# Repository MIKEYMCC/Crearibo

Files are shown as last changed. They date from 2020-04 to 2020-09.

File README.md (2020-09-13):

# Crearibo

CR-10 3D Printer Modification

This is a modification of the CR-10 S4 3D printer. It is a complete change to the Y X and Z axis to imitate the Prusa style printer specifically the Prusa MK2 and MK3 range. The main things provided by this modification are the parts for the Y and Z axis. THe X axis can be parts from the Prusa, Caribou and Bear range of pruse printers and modifications. There are 8mm and 10mm veriants of the Z axis. To be able to use the 10mm Z and or X axis currently you would need to use the Z and or X axis of the Caribou printer. I have included X motor and X idlers that have been modified to use the creality switches, these are for 8mm only, these were originally designed by Vekoj. 

The 10mm version does have a slightly smaller X axis at 295mm instead 300mm due to the way the X axis parts are designed.

To help with aligning the Y rods the holders edge should be 101mm from the edge of the extrusion with the endcap removed.

There is a template that can be printed to help drill holes in the CR-10 Y carriage so that the bearings can be attached.

Bill of Materials for 8mm

Z Axis:

6 x M4 10mm Cap Head Bolt FOR Z MOTOR MOUNTS

6 x M4 10mm Cap Head Bolt FOR Z TOP MOUNTS

16 x M4 Slot in T nuts

8 x M3 8mm Cap Head Bolt FOR MOTORS

2 x 535mmx8mm Linear Smooth Rods

4 x LM8UU Leanir Bearing

Y Axis:

2 x 12mmx500mm Linear Smooth Rods

3 x SCS12UU

12 x M5 10mm Cap Head Bolts FOR BEARING MOUNTING

5 x M3 10mm Cap Head Bolts

4 x M3 Locknuts FOR Y IDLER AND Y BELT HOLDER

4 x M4 10mm Cap Head Bolts FOR Y ROD HOLDERS

8 x M4 16mm Cap Head Bolts FOR Y ROD HOLDERS

16 x M4 Slot in T nuts

2 x M4 12mm Cap Head Bolts FOR Y IDLER

2 x M4 10mm Cap Head Bolts FOR Y MOTOR MOUNT

2 x M3 20mm Cap Head Bolts FOR Y IDLER ADJUSTER

1 x Microswitch for endstop

GT2 6mm Timing Belt

1 x 2GT 6mm Belt Timing Pulley 16T Toothless

1 x 2GT 6mm Belt Timing Pulley 16T Toothed to attach to motor

4 x Spacers for the bed to sit on.

4 x M3 12mm Cap Head Bolts for Y Carriage Belt Holder

4 x M3 Nut Square Y Carriage Belt Holder

X Axis:

2 x 415mmx8mm Linear Smooth Rods

3 x LM8UU Linear Bearinh

For the 10mm rod version you need 420mm long rods and bearings as specified by Caribou.

LCD Mounts:

2 x M4 10mm Cap Head Bolts

2 x M4 Slot in T nuts

Mosfet Case:

4 x M3 10mm Cap Head Bolts

4 x M3 8mm Cap Head Bolts

4 x M3 Square Nuts

4 x M3 Nut

1 x M4 10mm Cap Head Bolt

1 x M4 Slot in T nut

PSU case:

5 x M4 10mm Cap Head Bolts

5 x M4 Slot in T nut

4 x M4 8mm Counter Sunk Bolts

Bill of Materials for 10mm

Z Axis:

6 x M4 10mm Cap Head Bolt FOR Z MOTOR MOUNTS

8 x M4 10mm Cap Head Bolt FOR Z TOP MOUNTS

16 x M4 Slot in T nuts

8 x M3 8mm Cap Head Bolt FOR MOTORS

2 x 535mmx10mm Linear Smooth Rods

2 x LM10LUU Linear Bearing

Firmware

Is not currently provided as there can be differences in the mainboards used. I am personally using an SKR 1.4 Turbo and the firmware created by Chris Warkocki for the Bear can be used with changes to the axis lengths.

A lot of this mod has been made possible by the work of other groups and people namely Prusa, Caribou, Vekoj (thingiverse name) and Bear.

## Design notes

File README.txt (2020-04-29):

Crearibo Creality CR-10 Conversion to Linear Rods + 10mm Z/X version by MIKEYMCC on Thingiverse: https://www.thingiverse.com/thing:3143998

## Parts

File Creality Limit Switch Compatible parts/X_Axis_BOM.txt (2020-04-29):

X Axis:
2 x 415mmx8mm Linear Smooth Rods
3 x LM8UU Linear Bearing

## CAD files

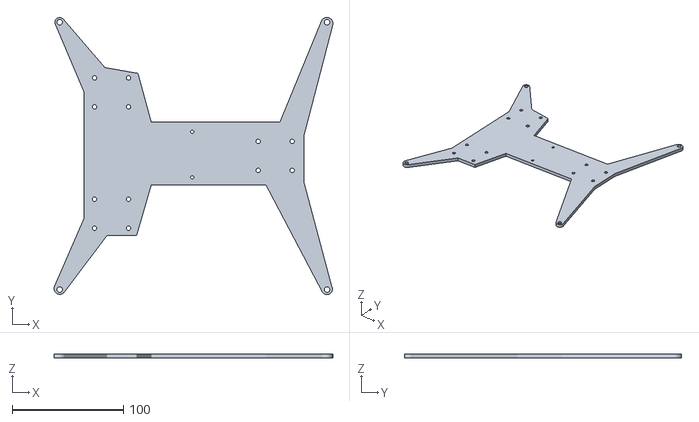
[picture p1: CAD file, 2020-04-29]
Bed Drilling Template/Bed_Template_Full.stl
250.4 x 248.8 x 4.00

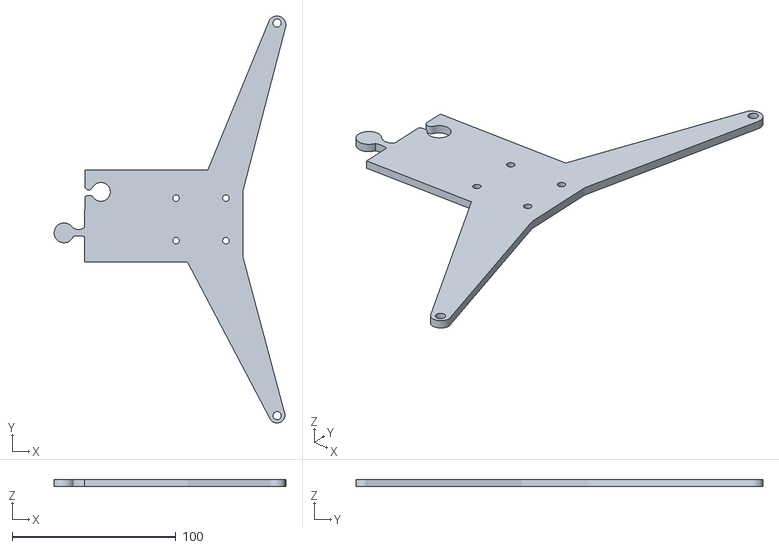
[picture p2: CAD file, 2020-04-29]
Bed Drilling Template/Bed_Template_2.stl
141.7 x 248.8 x 4.00

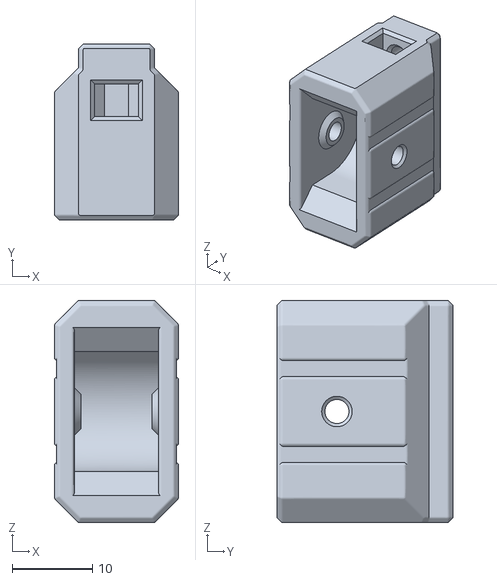
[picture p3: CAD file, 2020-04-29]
Creality Limit Switch Compatible parts/X-Idler_Tensioner_2.stl
15.5 x 22.0 x 27.7

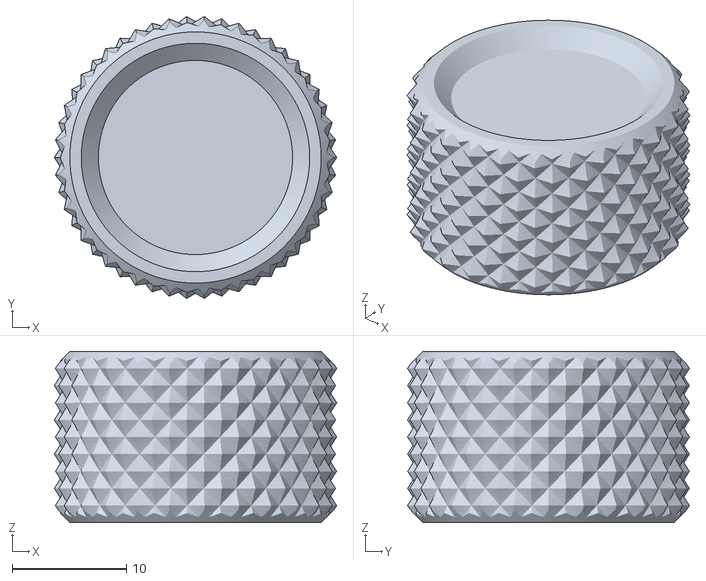
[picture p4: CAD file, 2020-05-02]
LCD/LCD knob.stl
24.7 x 24.7 x 15.0

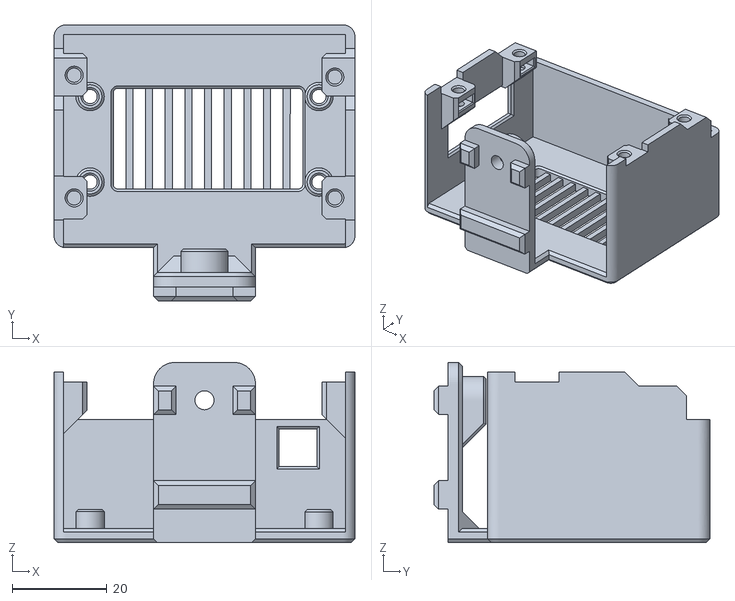
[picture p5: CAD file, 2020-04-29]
Mosfet Case/Mosfet_Case_Mount_New.stl
63.5 x 58.3 x 38.0

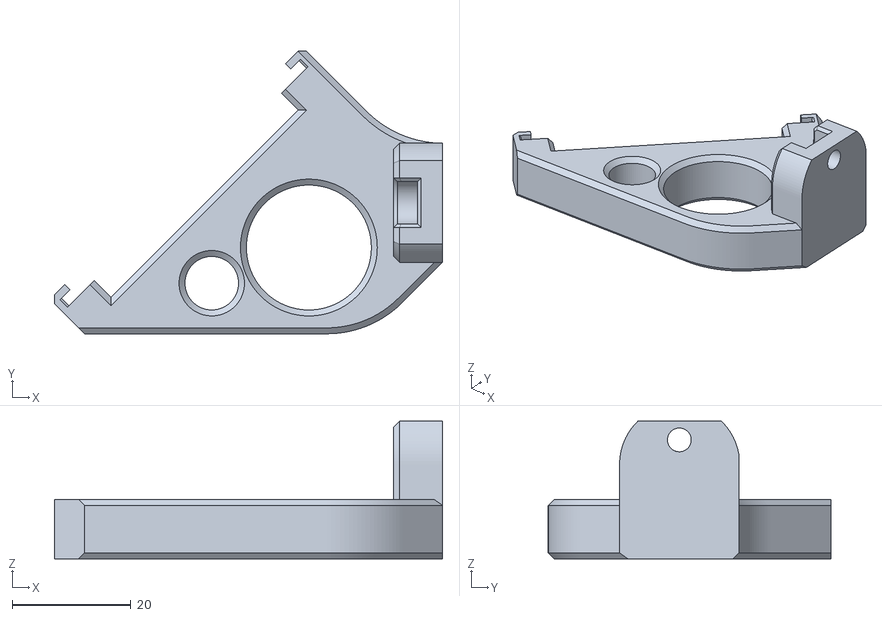
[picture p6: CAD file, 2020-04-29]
Prusa Compatible Parts/LCD_Support_B.stl
65.2 x 47.5 x 23.2

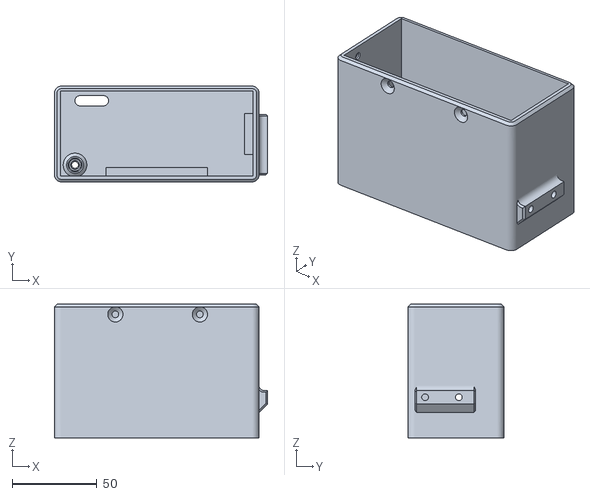
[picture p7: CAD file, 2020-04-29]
PSU Case/PSU_Case.stl
126.0 x 56.6 x 79.0

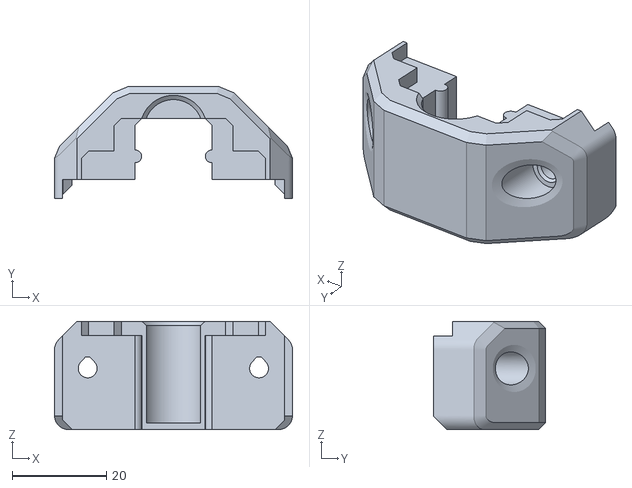
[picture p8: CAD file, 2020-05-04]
Y Axis/Y Rod Holder Cap x 4.stl
50.6 x 23.9 x 23.0

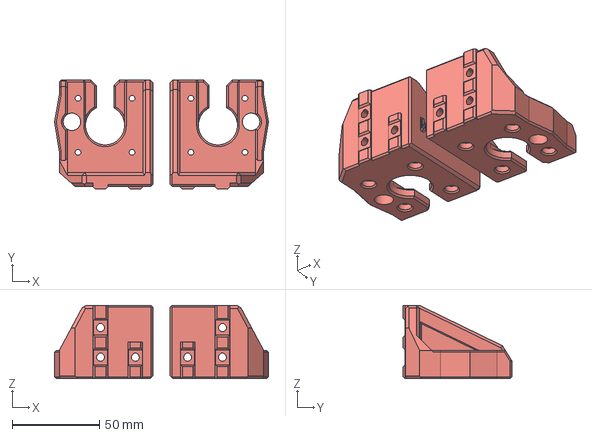
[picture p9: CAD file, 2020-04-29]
Z Axis 10mm/Creaibo_Z_Motor_10mm_v2.step
122.8 x 62.4 x 42.1 mm
Z Motor Left 10mm
Z Motor Right 10mm

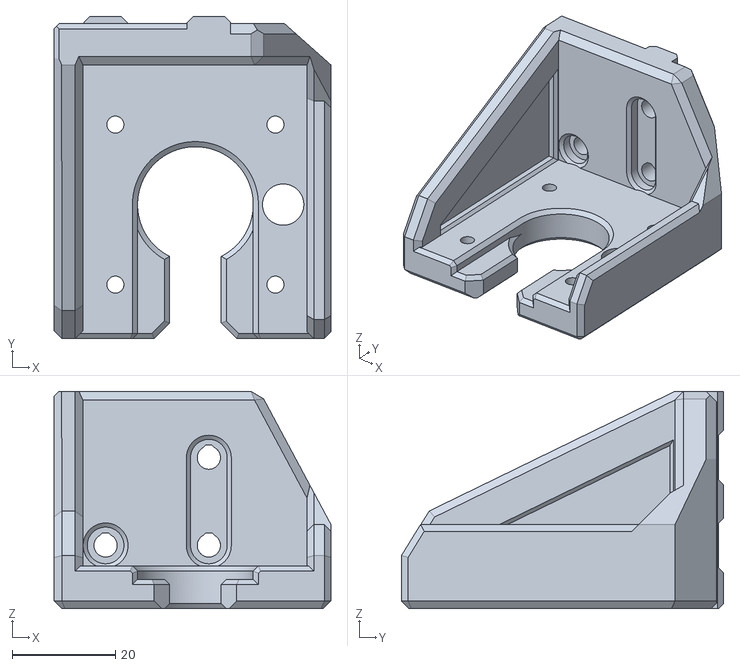
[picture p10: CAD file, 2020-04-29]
Z Axis 8mm/Z Motor Left 8mm.stl
53.7 x 62.4 x 42.1

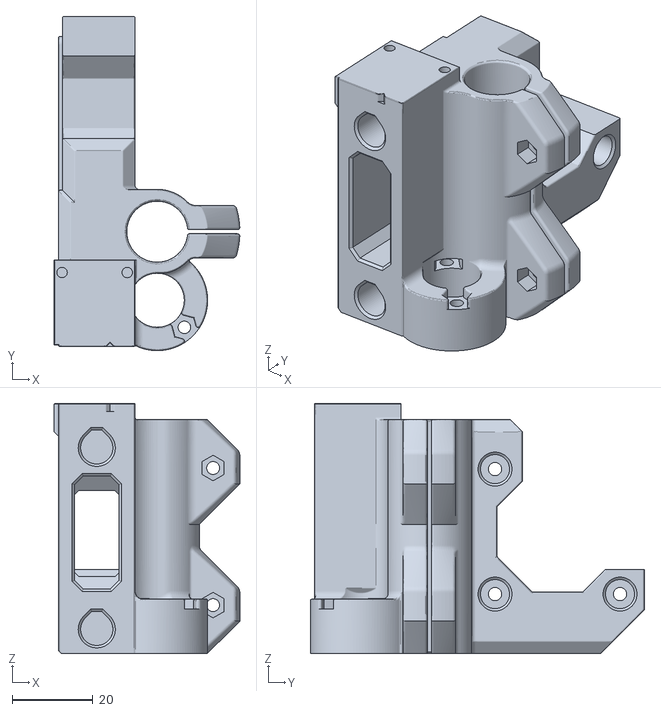
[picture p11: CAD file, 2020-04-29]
Creality Limit Switch Compatible parts/X-MotorHolder-2.21A_ZMK2_Creality_Switch.stl
46.0 x 82.9 x 62.0

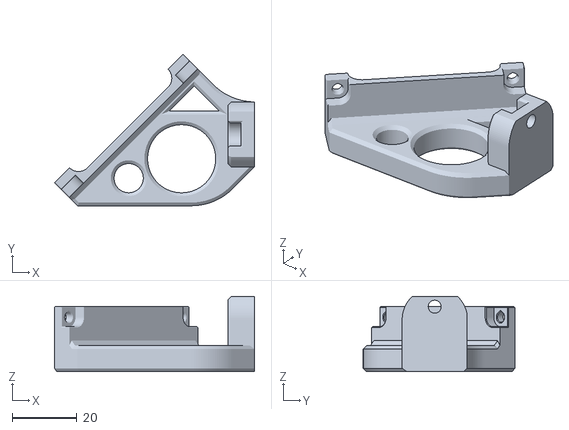
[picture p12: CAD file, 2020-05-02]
LCD/LCD Support B.stl
61.7 x 46.7 x 23.2

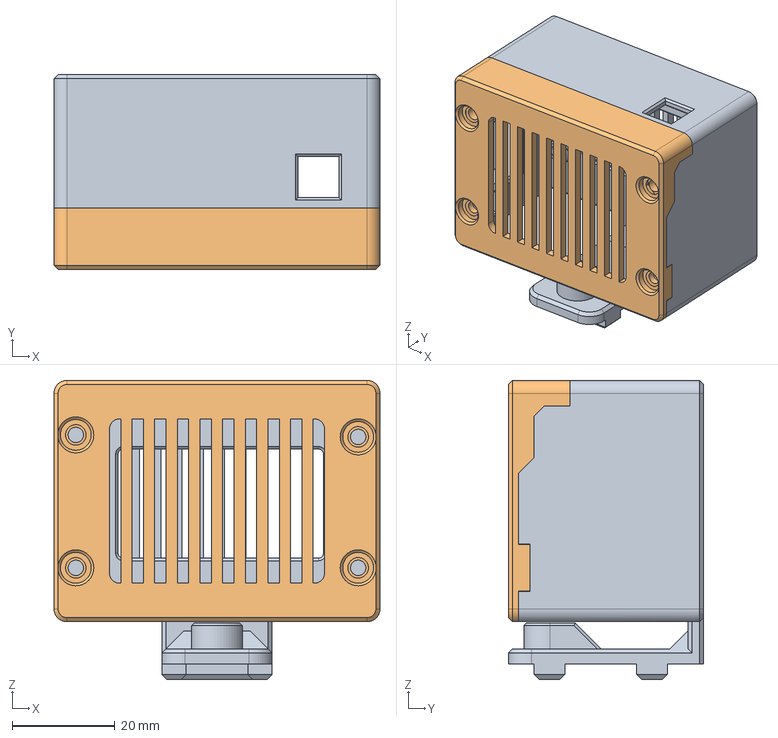
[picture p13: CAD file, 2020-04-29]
Mosfet Case/Mosfet_Case_V1.step
63.5 x 38.0 x 58.3 mm
Mosfet Case Mount
Mosfet Case Lid

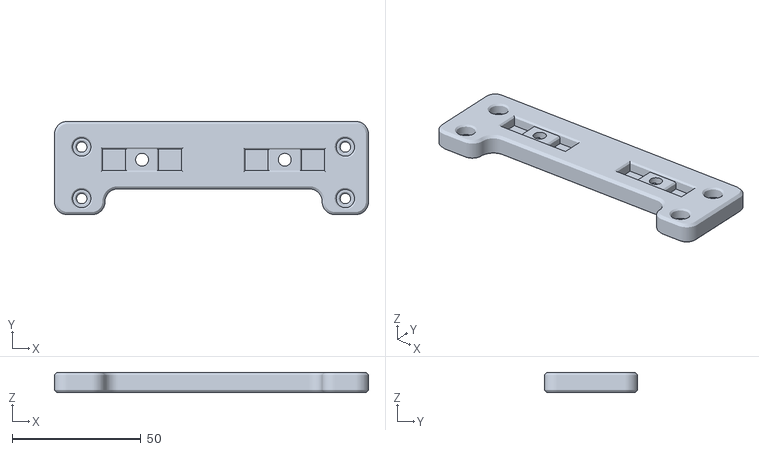
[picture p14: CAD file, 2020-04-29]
Prusa Compatible Parts/Zaribo_Einsy_Case_Adaptor.stl
121.9 x 36.2 x 7.95

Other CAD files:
PSU Case/PSU_Brace.stl
Y Axis/Y Rod Holder x 4.stl
Z Axis 10mm/Z_Top_Left_10mm.stl
Z Axis 8mm/Z Top Mounts 8mm.stl
Bed Drilling Template/Bed_Template_1.stl
Bed Drilling Template/Bed_Template_v1.step
Bed Drilling Template/CR_10_Mini_Bed_Template.STEP
Bed Drilling Template/CR_10_Mini_Bed_Template.STL
Creality Limit Switch Compatible parts/X-Idler-2.stl
LCD/LCD 2004 cover.stl
LCD/LCD Support A.stl
LCD/LCD-OLED-105 cover.stl
Mosfet Case/Mosfet_Box_Lid_New.stl
Mosfet Case/Mosfet_Case_Box_Zaribo.stl
Mosfet Case/Mosfet_Case_Box_Zaribo_Less_Holes.stl
Mosfet Case/Mosfet_Case_Lid_Zaribo.stl
Prusa Compatible Parts/LCD_Support_A.stl
Y Axis/Y Motor Mount Creality Switch.stl
Y Axis/Y Motor Mount No Limit Switch.stl
Y Axis/Y Motor Mount Prusa Switch.stl
Y Axis/Y Motor Spacer.stl
Y Axis/Y-Tensioner-Idler_2.11_Gates_20T_ID5_Screw_Version.STL
Y Axis/Y-Tensioner-Idler_2.11b_Gates_20T_ID5_Pin_Version.STL
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

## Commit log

2020-04-29 Update Z Axis BOM 10mm.txt
2020-05-02 Added updated full build step file
    This includes new LCD cases and mounts. There is a LCD case for OLED screens and a case for standard 2004 LCD's
2020-05-04 Updated rod holder cap to improve clearance and strength. Improved holes for printing on rod holders.
    [Y Rod Holder Cap x 4.stl, Y Rod Holder x 4.stl]
